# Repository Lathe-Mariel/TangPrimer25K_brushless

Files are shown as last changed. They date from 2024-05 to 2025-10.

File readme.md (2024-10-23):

# Overview
 This PCB board was made as a conversion board for Inverter Kit2 that is selling by CQ pub.
 Using this board, you can attach Tang Nano 25K(Sipeed) as an alternative to NUCLEO.
 There's Garber data made by KiCAD.

# BoM
型名 | アイテム（Item）|個数（Quantity）
---|---|---
　| 1608チップコンデンサ1μF | 1
　| 1608チップコンデンサ10μF | 1
　| 1608チップ抵抗220Ω | 8
　| 1608チップ抵抗4.7kΩ | 3
　| 1608チップ抵抗60.4Ω | 2
　| ダブルピンヘッダ（2x19列） | 2
　| JTAG用シングルピンヘッダ（1x4列） | 1
　| ジャンパ用シングルピンヘッダ（1x3列） | 1
　| RJ45ジャック | 1
TJA1441AT | CANトランシーバ | 1
SDCW3216-2-222TF | コモンモードチョークコイル | 1
SM24CANB-02HTG | | 1
TVGP01-G73BB with Gray cap | スイッチ | 2 
MCP3008-I/P | A-Dコンバータ | 1
2MS1-T1-B4-M2-Q-E | トグルスイッチ | 3
BP5293-50 | 5VDCDCコンバータ | 1

# FPGA Design
There's a sample project in sample directory.  
The project is files for Gowin EDA which is IDE for Gowin FPGA.
You can download Gowin EDA without any cost.

# Schematics

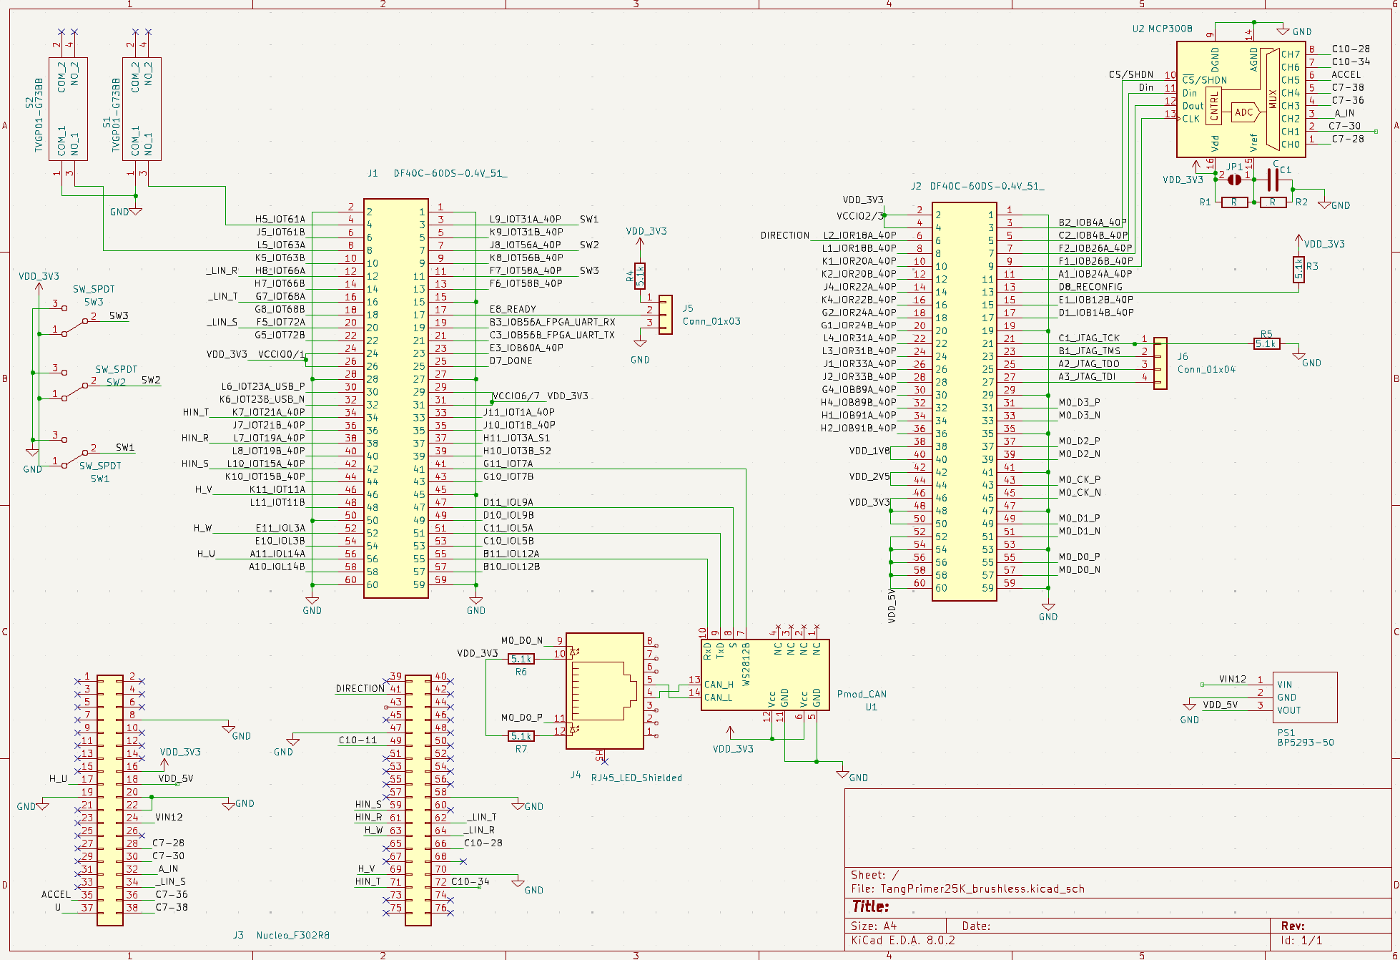
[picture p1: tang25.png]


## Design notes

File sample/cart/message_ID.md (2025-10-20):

Message ID | [0:7] | [8:15] | [16:23] | [24:31] |  [32:39] | [40:47] | [48:55] | [56:63]  
|--|--|--|--|--|--|--|--|--|
| 0x21 | - | - | - | - | - | - |SteeringWheelMessage? | - |
| 0x3d9 | - | battery | MSB of engine_speed | LSB of engine_speed | - | - | - | - |
| 0x3da | HazardON LeftTurnOn RightTurnOn 00000 | - | - | - | - | - | - | - |

| 0x3e9 | MSB of car_speed | LSB of car_speed | - | - | - | - | 000000  FuelLevelLow 0 | - |

| 0x191 | - | - | - | - | - | - | - | - |
ThrottlePosition

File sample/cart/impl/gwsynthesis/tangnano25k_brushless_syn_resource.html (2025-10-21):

# Hierarchy Module Resource

MODULE NAME | REG NUMBER | ALU NUMBER | LUT NUMBER | DSP NUMBER | BSRAM NUMBER | SSRAM NUMBER | ROM16 NUMBER
top (E:/git/TangPrimer25K_brushless/sample/cart/src/top.sv) | 189 | 148 | 214 | 1 | - | - | -
|--vehicle_data_generator_i (E:/git/TangPrimer25K_brushless/sample/cart/src/top.sv) | 22 | 18 | 21 | - | - | - | -
|--can_controller_i (E:/git/TangPrimer25K_brushless/sample/cart/src/top.sv) | - | - | - | - | - | - | -
|--can_sender_i (E:/git/TangPrimer25K_brushless/sample/cart/src/can_controller.sv) | 82 | - | 216 | - | - | - | -
|--can_synchronizer_i (E:/git/TangPrimer25K_brushless/sample/cart/src/can_controller.sv) | 42 | 20 | 105 | - | - | - | -
|--gw_gao_inst_0 (E:/git/TangPrimer25K_brushless/sample/cart/impl/gwsynthesis/RTL_GAO/gw_gao_top.v) | 286 | - | 318 | - | 55 | - | -

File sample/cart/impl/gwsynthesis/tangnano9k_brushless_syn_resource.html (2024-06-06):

# Hierarchy Module Resource

MODULE NAME | REG NUMBER | ALU NUMBER | LUT NUMBER | DSP NUMBER | BSRAM NUMBER | SSRAM NUMBER | ROM16 NUMBER
top (C:/Git/TangPrimer25K_brushless/sample/cart/src/top.sv) | 119 | 65 | 117 | 1 | - | - | -
|--vehicle_data_generator_i (C:/Git/TangPrimer25K_brushless/sample/cart/src/top.sv) | 22 | 18 | 20 | - | - | - | -
|--can_controller_i (C:/Git/TangPrimer25K_brushless/sample/cart/src/top.sv) | - | - | - | - | - | - | -
|--can_sender_i (C:/Git/TangPrimer25K_brushless/sample/cart/src/can_controller.sv) | 65 | - | 184 | - | - | - | -
|--can_synchronizer_i (C:/Git/TangPrimer25K_brushless/sample/cart/src/can_controller.sv) | 42 | 20 | 107 | - | - | - | -

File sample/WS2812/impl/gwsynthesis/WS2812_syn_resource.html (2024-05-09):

# Hierarchy Module Resource

MODULE NAME | REG NUMBER | ALU NUMBER | LUT NUMBER | DSP NUMBER | BSRAM NUMBER | SSRAM NUMBER
top (H:/git/TangPrimer25K_brushless/sample/WS2812/src/top.v) | 68 | 8 | 117 | - | - | -

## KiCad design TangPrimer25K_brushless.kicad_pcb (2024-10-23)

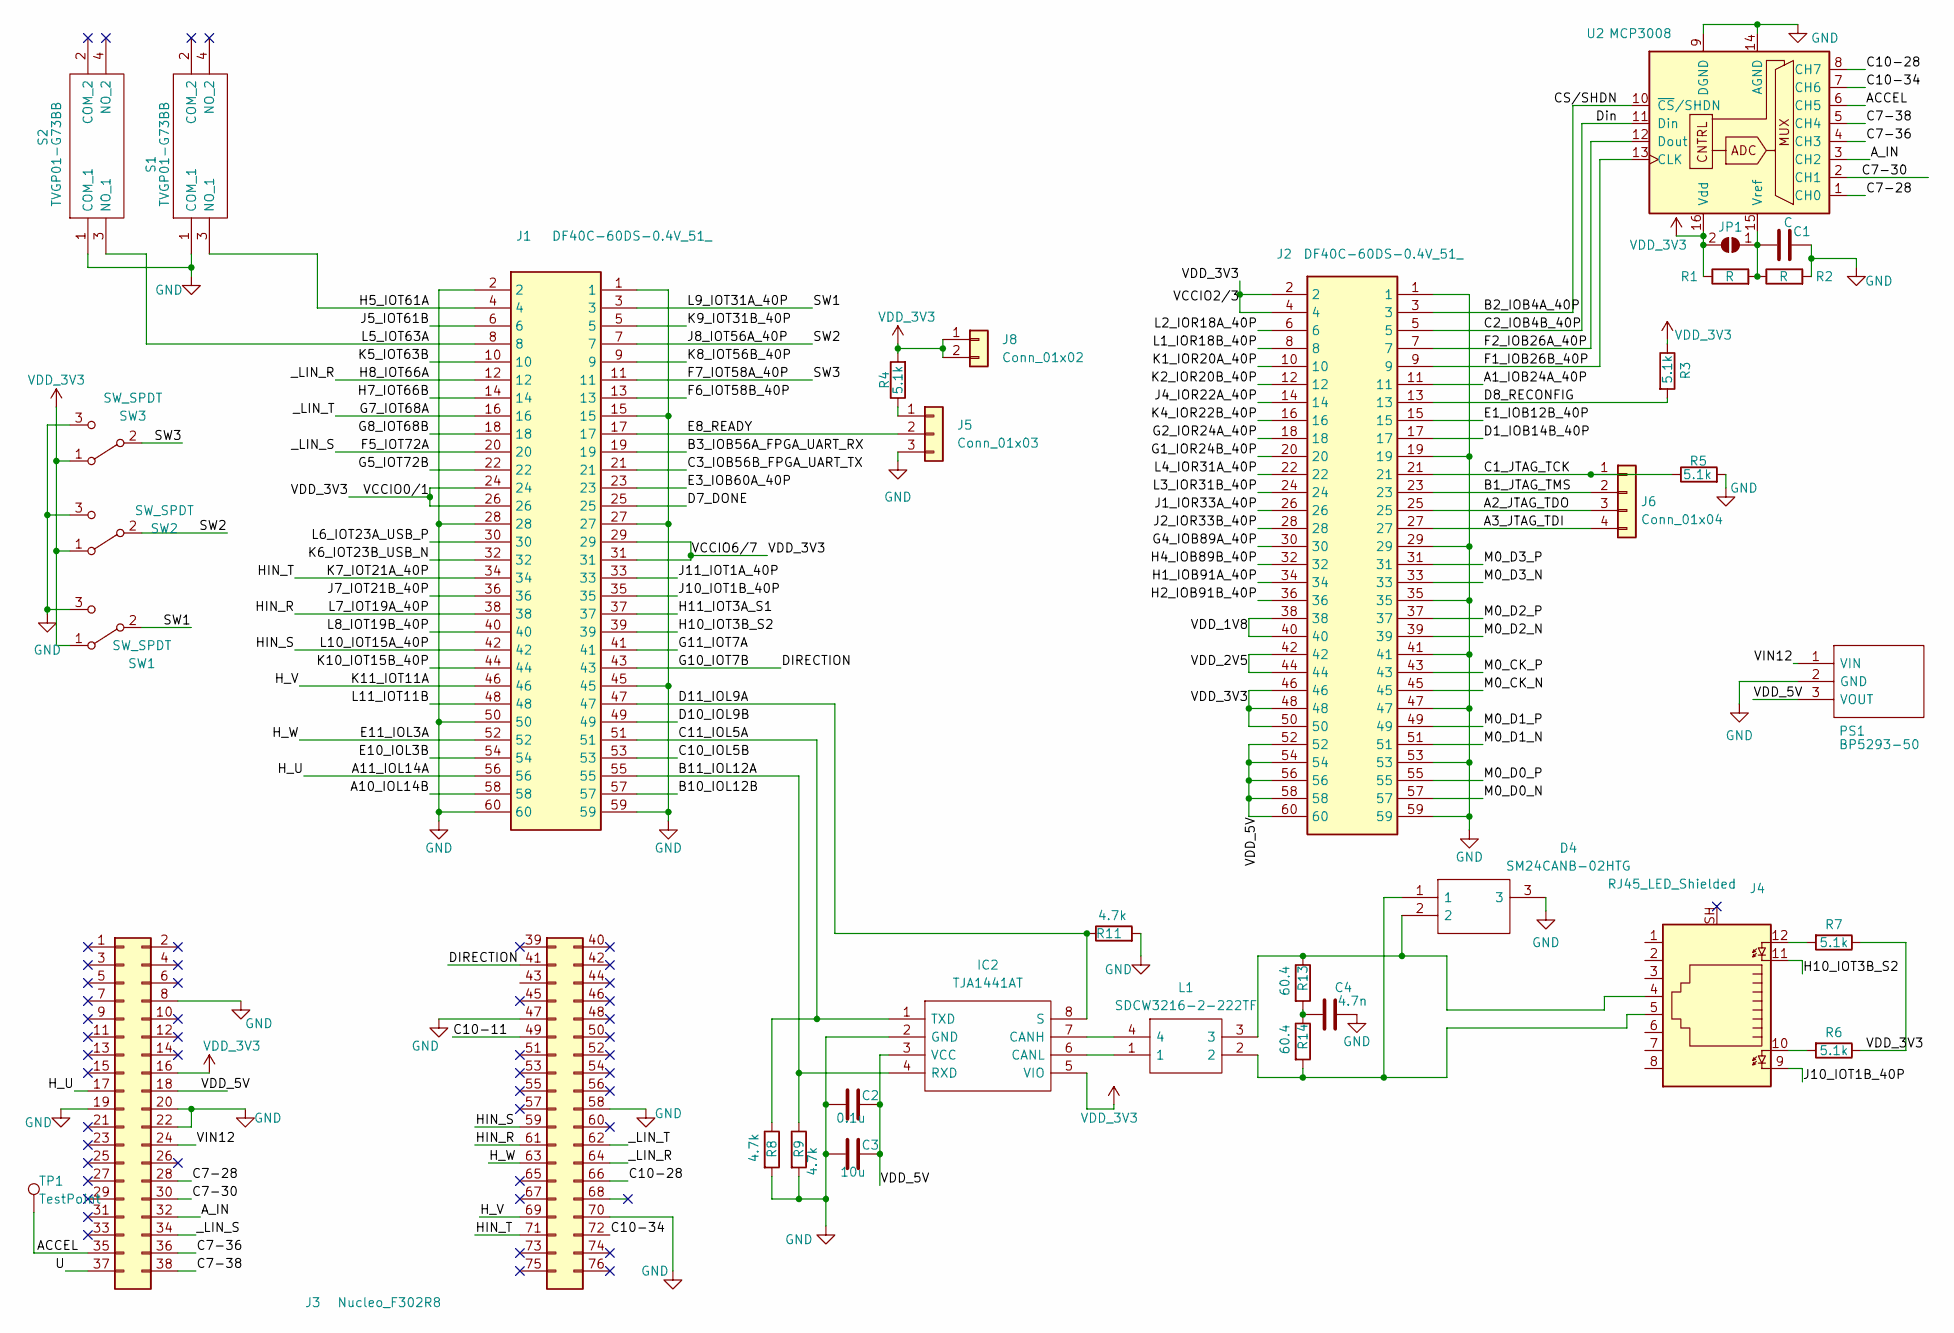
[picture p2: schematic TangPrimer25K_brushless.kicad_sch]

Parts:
C1: C; C_0603_1608Metric_Pad1.08x0.95mm_HandSolder
C2: 0.1u; C_0603_1608Metric_Pad1.08x0.95mm_HandSolder
C3: 10u; C_0603_1608Metric_Pad1.08x0.95mm_HandSolder
C4: 4.7n; C_0603_1608Metric_Pad1.08x0.95mm_HandSolder
D4: SM24CANB-02HTG; SM24CANB02HTG; Manufacturer_Part_Number SM24CANB-02HTG
IC2: TJA1441AT; SOIC127P600X175-8N; Manufacturer_Part_Number TJA1441AT
J1, J2: DF40C-60DS-0.4V_51_; Manufacturer_Part_Number DF40C-60DP-0.4V(51)
J3: Nucleo_F302R8; Nucleo
J4: RJ45_LED_Shielded; RJ45_Amphenol_RJHSE538X
J5: Conn_01x03; PinHeader_1x03_P2.54mm_Vertical
J6: Conn_01x04; PinHeader_1x04_P2.54mm_Vertical
J8: Conn_01x02; PinHeader_1x02_P2.54mm_Vertical
JP1: SolderJumper_2_Open; SolderJumper-2_P1.3mm_Open_TrianglePad1.0x1.5mm
L1: SDCW3216-2-222TF; SDCW32162222TF; Manufacturer_Part_Number SDCW3216-2-222TF
PS1: BP5293-50; TO254P570X1700X1780-3P; Manufacturer_Part_Number BP5293-50
R1, R2: R; R_0603_1608Metric_Pad0.98x0.95mm_HandSolder
R3, R4, R5, R6, R7: 5.1k; R_0603_1608Metric_Pad0.98x0.95mm_HandSolder
R8, R9, R11: 4.7k; R_0603_1608Metric_Pad0.98x0.95mm_HandSolder
R13, R14: 60.4; R_0603_1608Metric_Pad0.98x0.95mm_HandSolder
S1, S2: TVGP01-G73BB; TVGP01G73BB; Manufacturer_Part_Number TVGP01-G73BB
SW1, SW2, SW3: SW_SPDT; PinHeader_1x03_P2.54mm_Vertical
TP1: TestPoint; TestPoint_Pad_D1.5mm
U2: MCP3008; DIP-16_W7.62mm

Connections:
/A1_IOB24A_40P: J2.11
/A2_JTAG_TDO: J2.25, J6.3
/A3_JTAG_TDI: J2.27, J6.4
/A10_IOL14B: J1.58
/A11_IOL14A: J1.56, J3.17
/ACCEL: J3.35, TP1.1, U2.6 (CH5)
/A_IN: J3.32, U2.3 (CH2)
/B1_JTAG_TMS: J2.23, J6.2
/B2_IOB4A_40P: J2.3, U2.10 (~CS/SHDN)
/B3_IOB56A_FPGA_UART_RX: J1.19
/B10_IOL12B: J1.57
/B11_IOL12A: IC2.4 (RXD), J1.55, R9.1
/C1_JTAG_TCK: J2.21, J6.1, R5.1
/C2_IOB4B_40P: J2.5, U2.11 (Din)
/C3_IOB56B_FPGA_UART_TX: J1.21
/C7-28: J3.28, U2.1 (CH0)
/C7-30: J3.30, U2.2 (CH1)
/C7-36: J3.36, U2.4 (CH3)
/C7-38: J3.38, U2.5 (CH4)
/C10-11: J3.49
/C10-28: J3.66, U2.8 (CH7)
/C10-34: J3.72, U2.7 (CH6)
/C10_IOL5B: J1.53
/C11_IOL5A: IC2.1 (TXD), J1.51, R8.1
/D1_IOB14B_40P: J2.17
/D7_DONE: J1.25
/D8_RECONFIG: J2.13, R3.2
/D10_IOL9B: J1.49
/D11_IOL9A: IC2.8 (S), J1.47, R11.1
/DIRECTION: J1.43, J3.41
/E1_IOB12B_40P: J2.15
/E3_IOB60A_40P: J1.23
/E8_READY: J1.17, J5.2
/E10_IOL3B: J1.54
/E11_IOL3A: J1.52, J3.63
/F1_IOB26B_40P: J2.9, U2.13 (CLK)
/F2_IOB26A_40P: J2.7, U2.12 (Dout)
/F5_IOT72A: J1.20, J3.34
/F6_IOT58B_40P: J1.13
/F7_IOT58A_40P: J1.11, SW3.2 (B)
/G1_IOR24B_40P: J2.20
/G2_IOR24A_40P: J2.18
/G4_IOB89A_40P: J2.30
/G5_IOT72B: J1.22
/G7_IOT68A: J1.16, J3.62
/G8_IOT68B: J1.18
/G11_IOT7A: J1.41
/H1_IOB91A_40P: J2.34
/H2_IOB91B_40P: J2.36
/H4_IOB89B_40P: J2.32
/H5_IOT61A: J1.4, S1.3 (NO_1)
/H7_IOT66B: J1.14
/H8_IOT66A: J1.12, J3.64
/H10_IOT3B_S2: J1.39, J4.11
/H11_IOT3A_S1: J1.37
/HIN_R: J1.38, J3.61
/HIN_S: J1.42, J3.59
/HIN_T: J1.34, J3.71
/H_V: J1.46, J3.69
/J1_IOR33A_40P: J2.26
/J2_IOR33B_40P: J2.28
/J4_IOR22A_40P: J2.14
/J5_IOT61B: J1.6
/J7_IOT21B_40P: J1.36
/J8_IOT56A_40P: J1.7, SW2.2 (B)
/J10_IOT1B_40P: J1.35, J4.9
/J11_IOT1A_40P: J1.33
/K1_IOR20A_40P: J2.10
/K2_IOR20B_40P: J2.12
/K4_IOR22B_40P: J2.16
/K5_IOT63B: J1.10
/K6_IOT23B_USB_N: J1.32
/K8_IOT56B_40P: J1.9
/K9_IOT31B_40P: J1.5
/K10_IOT15B_40P: J1.44
/L1_IOR18B_40P: J2.8
/L2_IOR18A_40P: J2.6
/L3_IOR31B_40P: J2.24
/L4_IOR31A_40P: J2.22
/L5_IOT63A: J1.8, S2.3 (NO_1)
/L6_IOT23A_USB_P: J1.30
/L8_IOT19B_40P: J1.40
/L9_IOT31A_40P: J1.3, SW1.2 (B)
/L11_IOT11B: J1.48
/M0_CK_N: J2.45
/M0_CK_P: J2.43
/M0_D0_N: J2.57
/M0_D0_P: J2.55
/M0_D1_N: J2.51
/M0_D1_P: J2.49
/M0_D2_N: J2.39
/M0_D2_P: J2.37
/M0_D3_N: J2.33
/M0_D3_P: J2.31
/U: J3.37
/VDD_1V8: J2.38, J2.40
/VDD_2V5: J2.42, J2.44
/VDD_5V: C2.2, C3.2, IC2.3 (VCC), J2.52, J2.54, J2.56, J2.58, J2.60, J3.18, PS1.3 (VOUT)
/VIN12: J3.24, PS1.1 (VIN)
GND: C1.2, C2.1, C3.1, C4.2, D4.3, IC2.2 (GND), J1.1, J1.2, J1.15, J1.27, J1.28, J1.45, J1.50, J1.59, J1.60, J2.1, J2.19, J2.29, J2.35, J2.41, J2.47, J2.53, J2.59, J3.8, J3.19, J3.20, J3.22, J3.47, J3.58, J3.70, J5.3, PS1.2 (GND), R2.2, R5.2, R8.2, R9.2, R11.2, S1.1 (COM_1), S2.1 (COM_1), SW1.3 (C), SW2.3 (C), SW3.3 (C), U2.9 (DGND), U2.14 (AGND)
unnamed: C4.1, R13.2, R14.1
unnamed: D4.1, J4.5, L1.2, R14.2
unnamed: D4.2, J4.4, L1.3, R13.1
unnamed: IC2.7 (CANH), L1.4
unnamed: IC2.6 (CANL), L1.1
unnamed: J4.10, R6.2
unnamed: J4.12, R7.2
unnamed: J5.1, R4.1
unnamed: C1.1, JP1.1 (A), R1.2, R2.1, U2.15 (Vref)
VDD_3V3: IC2.5 (VIO), J1.24, J1.26, J1.29, J1.31, J2.2, J2.4, J2.46, J2.48, J2.50, J3.16, J8.1, J8.2, JP1.2 (B), R1.1, R3.1, R4.2, R6.1, R7.1, SW1.1 (A), SW2.1 (A), SW3.1 (A), U2.16 (Vdd)

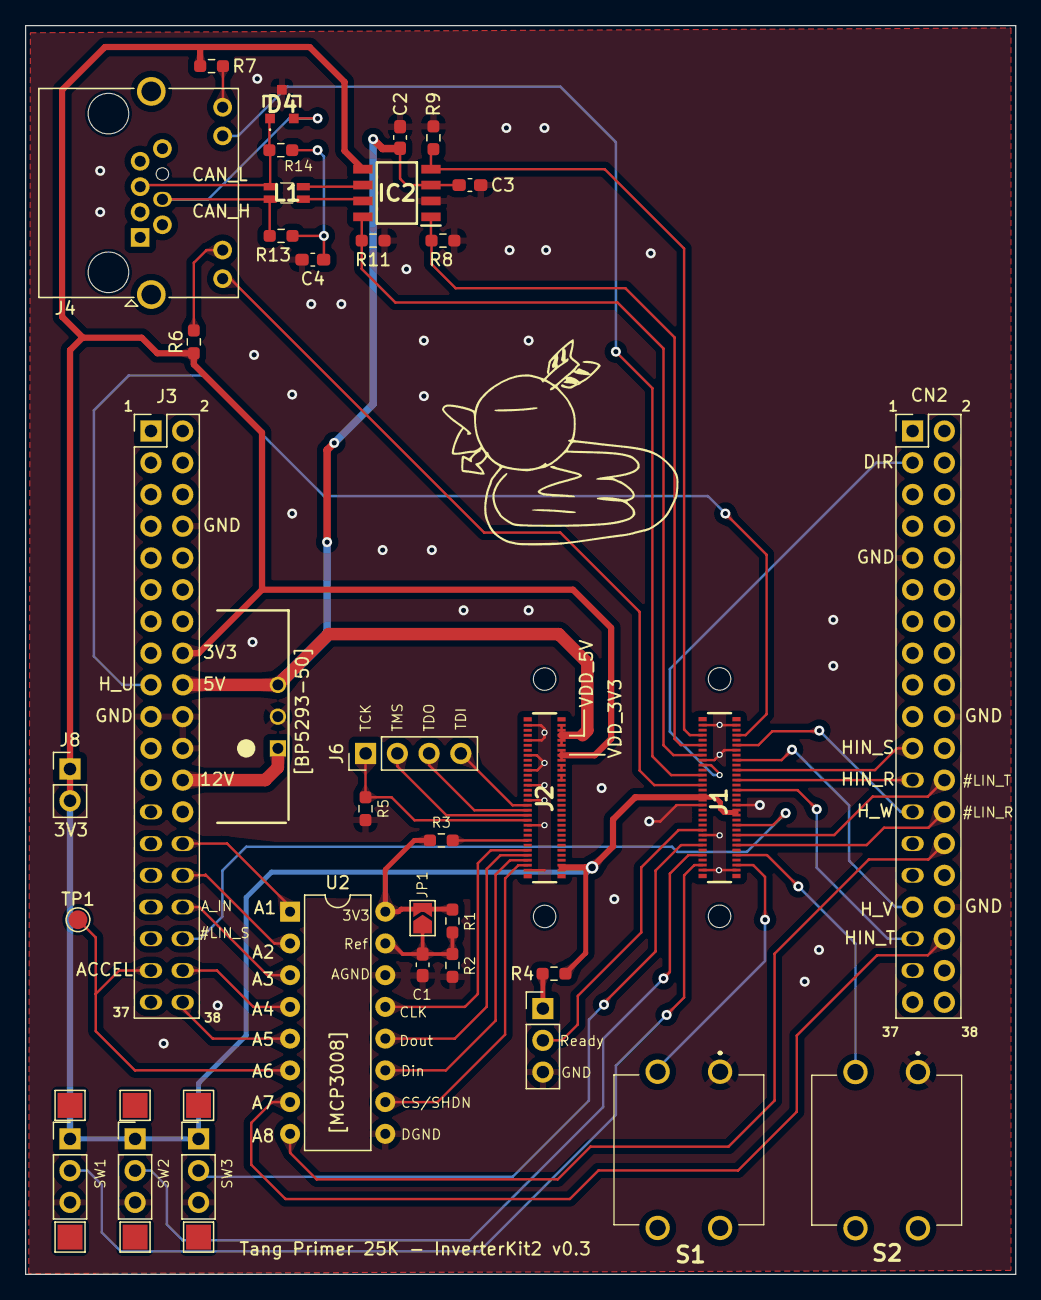
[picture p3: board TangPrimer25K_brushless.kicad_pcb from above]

Board: 2 copper layers, 79.2 x 99.9 mm, 35 parts (0 on the bottom side), 53 nets.

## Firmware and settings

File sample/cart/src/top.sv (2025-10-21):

`default_nettype none

module top (
  input  wire       clk,

  input wire[1:0] tacSW,     // tac SW1-2
  input wire[2:0] toggleSW,  //toggle SW 1-3
  input wire direction,
  input  wire[2:0] HS,       //HallSensor
  output wire AD_CLK,        // for MCP3008(ADC)
  output logic CS,           // for MCP3008
  output logic DIN,          //for MCP3008
  input reg DOUT,            //for MCP3008
  output logic HIN_R,        // Upper arm
  output logic HIN_S,
  output logic HIN_T,
  output logic _LIN_R,       //Lower arm
  output logic _LIN_S,
  output logic _LIN_T,
  output logic CAN_LED0,
  output logic CAN_LED1,
  output logic s,            //CAN Mode Select
  output logic txd,          //CAN データ送信線
  input wire rxd,            //CAN データ受信線
  output logic led_g,
  output logic led_y,
  output logic CAN_WS
);

  localparam CLK_FREQ_HZ    = 50_000_000;         // 入力クロック周波数
  localparam CAN_BITRATE_HZ = 500_000;            // CAN のビットレート
  localparam SLEEP_CYCLE    = CLK_FREQ_HZ / 100;  // データ送信後、スリープするcycle 数
  localparam ID_ENGINE_REV  = 11'h3D9;            // の送信ID
  localparam ID_CAR_SPEED   = 11'h3E9;            // モータ回転数の送信ID

  // Pmod CAN制御用，Normal mode に固定
  assign s = 1'b0;

  assign led_g = HS[0];
//  assign led_y = ele120_time[7];

  // モジュール間の接続に使用する変数
  wire status_warning;
  wire status_bus_off;
  logic [13:0] engine_rev;           // Motor revolution
  logic [8:0]  vehicle_speed;        // Motor current
  logic [7:0]  battery_value;        // Battery
  wire [63:0] stm_send_data_tdata;
  wire [10:0] stm_send_data_tid;
  wire [7:0]  stm_send_data_tkeep;
  wire        stm_send_data_tvalid;
  wire        stm_send_data_tready;
  wire [2:0]  stm_result_tdata;
  wire        stm_result_tvalid;
  wire        stm_result_tready;

  logic       controlCLK;
  logic       rotateCLK;
  logic[10:0] forcedRotationCounter;  //強制転流用インターバルカウンタ
  logic[2:0]  rotateState;            // 120°矩形波のmode
  logic duty;                         // current duty state
  logic[5:0]  dutyCounter;            // for duty control(relate to accel)
  logic _LR;                          // tmp value for lower arm value
  logic _LS;
  logic _LT;
  logic[15:0] processCounter;         // general counter 
  logic[9:0]  HSCounter;              // measurement hall sensor pulse
  logic[15:0]  OldprocessCounter;

  //logic[15:0]  ele120_time;
  logic[15:0] counter_per_cycle;      // counter per electrical angle 360degree
  logic[15:0] oldCounter_per_cycle;
  logic       isRotate;               // for control forcedRotation
  logic[2:0]  oldHS;                  // old Hall Sensor value
  logic[15:0]  delayAngleCounter;

  logic[2:0]  drive_mode;                   // BLDC drive mode

  logic[1:0]  tacSWpushed;            // flag for tac_SW1-4

  logic[9:0]  recieveADC;             // adc data from MCP3008
  logic[9:0]  accel;                  // accel value, that is transformed from recieveADC
  logic[9:0] speedMargin;

  logic[9:0]  analog_scan[8];         // storing adc(MCP3008, 10bits) values

  logic[11:0] dutyList[8]={'d1400, 'd1000, 'd800, 'd700, 'd620, 'd560, 'd520, 'd500};  //ドレミファインバータ風
  logic[2:0]  dutyPara;  //ドレミファインバータ制御用インデックス



///////// エンジン回転数と車速を送信するモジュール /////////
  vehicle_data_generator #(
    .SLEEP_CYCLE(SLEEP_CYCLE),
    .ID_ENGINE_REV(ID_ENGINE_REV),
    .ID_CAR_SPEED(ID_CAR_SPEED)
  ) vehicle_data_generator_i (
    .stm_send_data_out_tdata (stm_send_data_tdata),
    .stm_send_data_out_tid   (stm_send_data_tid),
    .stm_send_data_out_tkeep (stm_send_data_tkeep),
    .stm_send_data_out_tvalid(stm_send_data_tvalid),
    .stm_send_data_out_tready(stm_send_data_tready),
    .stm_result_in_tdata     (stm_result_tdata),
    .stm_result_in_tvalid    (stm_result_tvalid),
    .stm_result_in_tready    (stm_result_tready),
    .*
  );

  ///////// CAN コントローラ /////////
  can_controller #(
    .CLK_FREQ_HZ(CLK_FREQ_HZ),
    .CAN_BITRATE_HZ(CAN_BITRATE_HZ)
  ) can_controller_i (
    .stm_send_data_in_tdata (stm_send_data_tdata),
    .stm_send_data_in_tid   (stm_send_data_tid),
    .stm_send_data_in_tkeep (stm_send_data_tkeep),
    .stm_send_data_in_tvalid(stm_send_data_tvalid),
    .stm_send_data_in_tready(stm_send_data_tready),
    .stm_result_out_tdata   (stm_result_tdata),
    .stm_result_out_tvalid  (stm_result_tvalid),
    .stm_result_out_tready  (stm_result_tready),
    .*
  );


  always @(posedge controlCLK)begin

// forced rotation
    if(isRotate == 0)begin
      if(forcedRotationCounter == 0)begin
        rotateState <= (rotateState + 1) % 6;
      end
      forcedRotationCounter <= forcedRotationCounter + 1;
    end else begin

// rotation by hall sensor
      if(toggleSW[0])begin     //CW  //direction
        case(drive_mode)
          3'd1: rotateState = 3'd4;
          3'd2: rotateState = 3'd0;
          3'd3: rotateState = 3'd5;
          3'd4: rotateState = 3'd2;
          3'd5: rotateState = 3'd3;
          3'd6: rotateState = 3'd1;
        endcase
      end else begin         //CCW
        case(drive_mode)
          3'd1: rotateState = 3'd1;
          3'd2: rotateState = 3'd3;
          3'd3: rotateState = 3'd2;
          3'd4: rotateState = 3'd5;
          3'd5: rotateState = 3'd0;
          3'd6: rotateState = 3'd4;
        endcase
      end
    end

    processCounter <= processCounter + 1;

// check sw //change something to display
    if(processCounter % 4096 == 0)begin
      if(HSCounter > 84)begin
        dutyPara <= 'd7;
      end else if(HSCounter > 68)begin
        dutyPara <= 'd6;
      end else if(HSCounter > 54)begin
        dutyPara <= 'd5;
      end else if(HSCounter > 40)begin
        dutyPara <= 'd4;
      end else if(HSCounter > 28)begin
        dutyPara <= 'd3;
      end else if(HSCounter > 18)begin
        dutyPara <= 'd2;
      end else if(HSCounter > 10)begin
        dutyPara <= 'd1;
      end else begin
        dutyPara <= 'd0;
      end

//      oldHSCounter <= HSCounter;
      engine_rev <= HSCounter * 10'd3;
      HSCounter <= 0;

      if(HSCounter > 0)begin
        isRotate <= 'b1;
      end else begin
        isRotate <= 'b0;
        forcedRotationCounter <= 0;
      end
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

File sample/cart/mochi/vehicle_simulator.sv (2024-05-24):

`default_nettype none

// エンジン回転数と車速をシミュレーションするモジュール
module vehicle_simulator #(
  parameter CLK_FREQ_HZ = 50_000_000  // 入力クロック周波数
) (
  input  wire         clk,          // クロック入力
  output logic [13:0] engine_rev,   // エンジン回転数出力
  output logic [8:0]  vehicle_speed // 車速出力
);

  ///////// 1 ms タイマー /////////
  logic [31:0] timer = 'd0;
  wire signal_ms = (timer == CLK_FREQ_HZ / 1_000 - 1);
  always_ff @ (posedge clk) begin
    if (signal_ms) begin
      timer <= 'd0;
    end else begin
      timer <= timer + 'd1;
    end
  end

  ///////// ステートマシン /////////
  localparam STATE_IDLE = 0;
  localparam STATE_LAUNCH_CONTROL = 1;
  localparam STATE_CLUTCH_CONTROL = 2;
  localparam STATE_GEAR_1ST = 3;
  localparam STATE_GEAR_2ND = 4;
  localparam STATE_GEAR_3RD = 5;
  localparam STATE_GEAR_4TH = 6;
  localparam STATE_BRAKE = 7;
  localparam STATE_NUM = 8;
  logic [$clog2(STATE_NUM)-1:0] state = STATE_IDLE;
  logic [15:0] wait_counter = 'd0;
  always_ff @ (posedge clk) begin
    if (signal_ms) begin
      case(state)
        STATE_IDLE: begin
          engine_rev <= 'd2000;
          vehicle_speed <= 'd0;
          if (wait_counter == 'd999) begin
            wait_counter <= 'd0;
            state <= STATE_LAUNCH_CONTROL;
          end else begin
            wait_counter <= wait_counter + 'd1;
          end
        end
        STATE_LAUNCH_CONTROL: begin
          engine_rev <= 'd6000;
          vehicle_speed <= 'd0;
          if (wait_counter == 'd999) begin
            wait_counter <= 'd0;
            state <= STATE_CLUTCH_CONTROL;
          end else begin
            wait_counter <= wait_counter + 'd1;
          end
        end
        STATE_CLUTCH_CONTROL: begin
          engine_rev <= 'd5000;
          if (vehicle_speed >= 'd50) begin
            wait_counter <= 'd0;
            state <= STATE_GEAR_1ST;
          end else if (wait_counter == 'd30) begin
            wait_counter <= 'd0;
            vehicle_speed <= vehicle_speed + 'd1;
          end else begin
            wait_counter <= wait_counter + 'd1;
          end
        end
        STATE_GEAR_1ST: begin
          if (engine_rev >= 'd7000) begin
            engine_rev <= 'd5000;
            wait_counter <= 'd0;
            state <= STATE_GEAR_2ND;
          end else if (wait_counter == 'd30) begin
            wait_counter <= 'd0;
            engine_rev <= engine_rev + 'd100;
            vehicle_speed <= vehicle_speed + 'd1;
          end else begin
            wait_counter <= wait_counter + 'd1;
          end
        end
        STATE_GEAR_2ND: begin
          if (engine_rev >= 'd7000) begin
            engine_rev <= 'd5000;
            wait_counter <= 'd0;
            state <= STATE_GEAR_3RD;
          end else if (wait_counter == 'd40) begin
            wait_counter <= 'd0;
            engine_rev <= engine_rev + 'd75;
            vehicle_speed <= vehicle_speed + 'd1;
          end else begin
            wait_counter <= wait_counter + 'd1;
          end
        end
        STATE_GEAR_3RD: begin
          if (engine_rev >= 'd7000) begin
            engine_rev <= 'd5000;
            wait_counter <= 'd0;
            state <= STATE_GEAR_4TH;
          end else if (wait_counter == 'd50) begin
            wait_counter <= 'd0;
            engine_rev <= engine_rev + 'd45;
            vehicle_speed <= vehicle_speed + 'd1;
          end else begin
            wait_counter <= wait_counter + 'd1;
          end
        end
        STATE_GEAR_4TH: begin
          if (engine_rev >= 'd7000) begin
            // engine_rev <= 'd5000;
            wait_counter <= 'd0;
            state <= STATE_BRAKE;
          end else if (wait_counter == 'd60) begin
            wait_counter <= 'd0;
            engine_rev <= engine_rev + 'd30;
            vehicle_speed <= vehicle_speed + 'd1;
          end else begin
            wait_counter <= wait_counter + 'd1;
          end
        end
        STATE_BRAKE: begin
          if (vehicle_speed <= 'd0) begin
            wait_counter <= 'd0;
            state <= STATE_IDLE;
          end else if (wait_counter == 'd30) begin
            wait_counter <= 'd0;
            vehicle_speed <= vehicle_speed - 'd1;
            if (engine_rev > 'd2020) begin
              // engine_rev <= engine_rev - 'd20;
              engine_rev <= engine_rev - 'd30;
            end else begin
              engine_rev <= 'd2000;
            end
          end else begin
            wait_counter <= wait_counter + 'd1;
          end
        end
        default:
          state <= STATE_IDLE;
      endcase
    end
  end

endmodule

`default_nettype wire

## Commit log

2024-05-24 can design add
    [device.cfg]
2025-09-10 adding function advance angle controll
    [device.cfg]
2025-09-13 advance agngle
    [device.cfg]
2025-09-13 advance angle control
    [device.cfg]
2025-09-14 advance angle
    [device.cfg]
2025-09-25 start parameter
    [device.cfg]
2025-10-21 advance degree adjustment
    [device.cfg]
